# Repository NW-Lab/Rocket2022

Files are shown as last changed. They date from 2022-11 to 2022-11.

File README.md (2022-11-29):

# Rocket2022
発射実験用

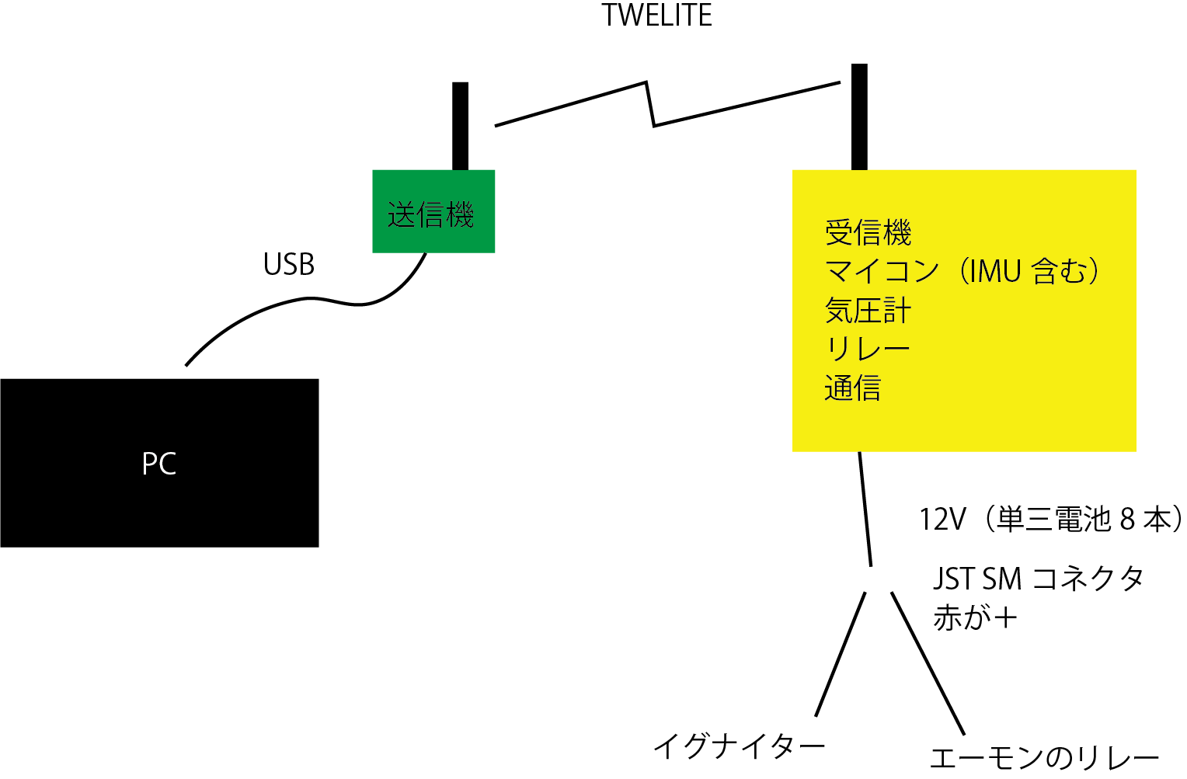
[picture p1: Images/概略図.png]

<br/>
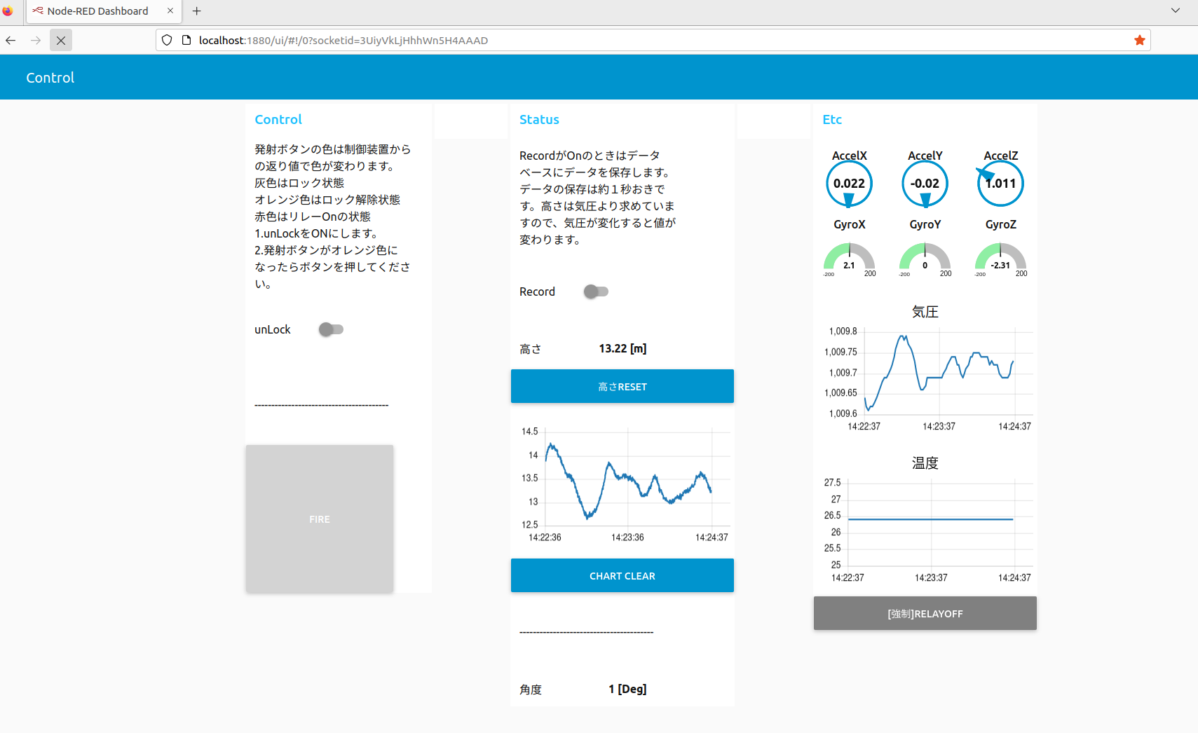
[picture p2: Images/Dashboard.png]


## 使用機材
### PC側
|物品名|規格|URL|備考|
| --- | --- | ---| --- |
|PC|Ubuntu 22.04+NodeRed+InfluxDB| |USB端子があれば|
|TWELITE|TWELITE DIP|https://mono-wireless.com/jp/products/TWE-Lite-DIP/index.html| |
|TWELITE|TWELITE R2|https://mono-wireless.com/jp/products/TWE-LITE-R/index.html| |
|SMA変換ケーブル|MW-C-UJ-10-1|https://mono-wireless.com/jp/products/TWE-ANTENNAS/cables/index.html| |
|防水可倒式アンテナ|MW-A-D114|https://mono-wireless.com/jp/products/TWE-ANTENNAS/dipole/outdoor-ant.html| |
|ケース|タカチ SW‐85B|https://akizukidenshi.com/catalog/g/gP-12472/| |

TWELITEは、普通にUART+適当な変換器(3.3V)でもよかったかも。（TWELITE Stageを設定すると、/dev/ttyUSB0 が見えなくなる。ので設定ソフトとの共用は難しい。無難に設定はWindows機を用意した方が簡単

### ロケット側
|物品名|規格|URL|備考|
| --- | --- | --- | --- |
|マイコン|Seeed Studio XIAO nRF52840 Sense|https://www.seeedstudio.com/Seeed-XIAO-BLE-Sense-nRF52840-p-5253.html|IMU入ってるし、小さいのでこれを選択。あと3.3Vなので（M5は5V)|
|マイコン拡張基板|Seeeduino Xiao用Grove|https://wiki.seeedstudio.com/Grove-Shield-for-Seeeduino-XIAO-embedded-battery-management-chip/|折って4口までにした|
|気圧計|Grove - High Precision Barometric Pressure Sensor (DPS310)|https://www.seeedstudio.com/Grove-High-Precision-Barometer-Sensor-DPS310-p-4397.html|高度が測れる精度が欲しかった|
|リレー|Grobe　Relay|https://www.seeedstudio.com/Grove-Relay.html|3.3Vで動くリレー|
|TWELITE|TWELITE UART|https://mono-wireless.com/jp/products/twelite-uart/index.html|Groveケーブルをはんだ付け|
|SMA変換ケーブル|MW-C-UJ-10-1|https://mono-wireless.com/jp/products/TWE-ANTENNAS/cables/index.html||
|防水可倒式アンテナ|MW-A-D114|https://mono-wireless.com/jp/products/TWE-ANTENNAS/dipole/outdoor-ant.html||
|マイコン用電源（昇圧回路）|電池基板A4-2Unit|https://www.switch-science.com/products/6759|マイコン動作の5Vを簡単にしたかったのでUSBでつないだ|
|発火用電池ボックス|単3x8|https://akizukidenshi.com/catalog/g/gP-00312/||
|バッテリスナップ| |https://akizukidenshi.com/catalog/g/gP-00312/||
|ケース|タカチ　BCPC091208T|https://www.takachi-el.co.jp/products/BCPC||

ねじ少々(M2、M3)

気圧がI2C（D4,D5）、リレーがGPIO（D1,D2）、TWELITEがUART（D6,D7）に接続する。

マイコンと拡張基板が結構ゆるゆるだったのでマスキングテープで補強した。

組み立て<br/>
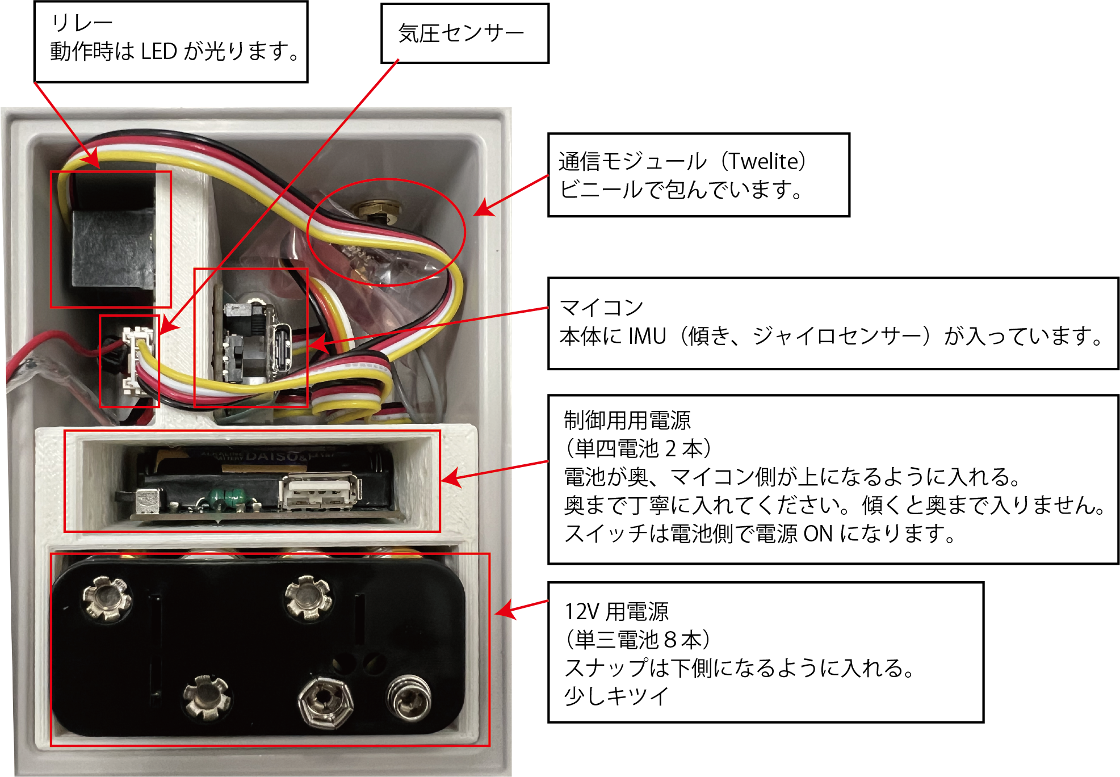
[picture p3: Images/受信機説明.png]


## 開発環境
### PC側
- Ubuntu 20.04LTS
- Node-Red
  - node-red-dashboard
  - node-red-node-serialport
  - node-red-contrib-influxdb
- InfluxDB(OSS) https://www.influxdata.com/
- 
### ロケット側
#### Arduino 1.8.19
Boardは、"Seeed nRF52 mbed enable boards --> Seeed XIAO BLE sense"を利用する。ただし、Board両方Installする必要あり。　https://wiki.seeedstudio.com/XIAO_BLE/

Libraryは以下の2つ
-   Seeed_Arduino_LSM6DS3 Library　https://github.com/Seeed-Studio/Seeed_Arduino_LSM6DS3
-   Adafruit DPS310

## リンク

XIAO BLE https://wiki.seeedstudio.com/XIAO_BLE/

植松電機　https://uematsudenki.com/モデルロケット自作コントローラー/

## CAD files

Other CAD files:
Fusion360/受信機ケース仕切り.f3d
Fusion360/送信機のアンテナ.f3d

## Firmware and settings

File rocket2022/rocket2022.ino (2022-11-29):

#include <Scheduler.h>
#include "LSM6DS3.h"
#include <Adafruit_DPS310.h>
#include "Wire.h"

LSM6DS3 myIMU(I2C_MODE, 0x6A);    //I2C device address 0x6A

Adafruit_DPS310 myDps;
Adafruit_Sensor *dps_temp = myDps.getTemperatureSensor();
Adafruit_Sensor *dps_pressure = myDps.getPressureSensor();

float pressureInit;

//#define mySerial2 SerialUSB
#define mySerial Serial1
#define myRelay D1

//Status
bool sLock = true;
byte RelayCount = 0;
int SensorCount = 0;
byte PcCount = 0;
float sRSSI = 0.0;
float sBattery = 0.0;

//Function
float P2High(float pressure, float pressureInit, float temp) {
  return ((pow((pressureInit / pressure), 1 / 5.257) - 1.0) * (temp + 273.15)) / 0.0065;
}

void setup() {
  int16_t ret;
  mySerial.begin(115200);
  //mySerial2.begin(115200);
  pinMode(myRelay, OUTPUT); digitalWrite(myRelay, LOW);

  pinMode(LEDR, OUTPUT); digitalWrite(LEDR, HIGH);
  pinMode(LEDG, OUTPUT); digitalWrite(LEDG, HIGH);
  pinMode(LEDB, OUTPUT); digitalWrite(LEDB, HIGH);

  if (myIMU.begin() != 0) {
    //mySerial2.println("Device(IMU) error");
  } else {
    //mySerial2.println("Device(IMU) OK!");
  }

  if (! myDps.begin_I2C()) {
    //mySerial2.println("Failed to find DPS");
    while (1) yield();
  }
  //mySerial2.println("DPS310 OK!");
  sensors_event_t  pressure_event;
  myDps.configurePressure(DPS310_128HZ, DPS310_8SAMPLES);
  myDps.configureTemperature(DPS310_128HZ, DPS310_8SAMPLES);
  while ( !myDps.pressureAvailable()) {
    delay(1);
  }
  delay(1000);
  dps_pressure->getEvent(&pressure_event);
  pressureInit = pressure_event.pressure;

  // put your setup code here, to run once:
  Scheduler.startLoop(loop_alive_LED);
  Scheduler.startLoop(loop_Rcv);
  Scheduler.startLoop(loop_Relay);
}

void loop() {
  int16_t ret;
  sensors_event_t temp_event, pressure_event;
  float pressure, temp;
  //Sensor用

/***  
  float ax=myIMU.readFloatAccelX();
  float ay=myIMU.readFloatAccelY();
  float az=myIMU.readFloatAccelZ();
  float gx=myIMU.readFloatGyroX();
  float gy=myIMU.readFloatGyroY();
  float gz=myIMU.readFloatGyroZ();
**/
  float ax=-1.0*myIMU.readFloatAccelY();
  float ay=myIMU.readFloatAccelZ();
  float az=-1.0*myIMU.readFloatAccelX();
  float gx=-1.0*myIMU.readFloatGyroY();
  float gy=myIMU.readFloatGyroZ();
  float gz=-1.0*myIMU.readFloatGyroX();
  
  mySerial.print("{");
  mySerial.print("\"lock\":");
  if (sLock)mySerial.print("true");
  else mySerial.print("false");
  mySerial.print(",\"RelayOn\":");
  if (RelayCount > 0)mySerial.print("true");
  else mySerial.print("false");
  mySerial.println("}");

  mySerial.print("{\"AccelX\":");
  mySerial.print(ax, 3);
  mySerial.print(',');

  mySerial.print("\"AccelY\":");
  mySerial.print(ay, 3);
  mySerial.print(',');

  mySerial.print("\"AccelZ\":");
  mySerial.print(az, 3);
  mySerial.println("}");

  mySerial.print("{\"GyroX\":");
  mySerial.print(gx, 3);
  mySerial.print(',');

  mySerial.print("\"GyroY\":");
  mySerial.print(gy, 3);
  mySerial.print(',');

  mySerial.print("\"GyroZ\":");
  mySerial.print(gz, 3);
  mySerial.println("}");

  while (!myDps.temperatureAvailable() || !myDps.pressureAvailable()) {
    delay(1);
  }
  myDps.getEvents(&temp_event, &pressure_event);
  temp = temp_event.temperature;
  pressure = pressure_event.pressure;

  mySerial.print("{\"Temperature\":");
  mySerial.print(temp, 1);
  mySerial.print(',');

  mySerial.print("\"Pressure\":");
  mySerial.print(pressure, 2);
  mySerial.print(',');

  mySerial.print("\"Height\":");
  mySerial.print(P2High(pressure, pressureInit, temp), 2);
  mySerial.println("}");
  /**
    mySerial.print("{\"RSSI\":");
    mySerial.print(sRSSI, 2);
    mySerial.print(',');

    mySerial.print("\"Battery\":");
    mySerial.print(sBattery, 2);

    mySerial.println("}");
    **/
  delay(100);
}
void loop_alive_LED() {
  // 内蔵LEDは、PullUpされているので反転動作
  if (sLock) {  //ロックされている場合は緑
    digitalWrite(LEDG, LOW);
    digitalWrite(LEDR, HIGH);
    delay(100);
    if (PcCount != 0)digitalWrite(LEDG, HIGH);
    delay(100);
  }
  else {  //ロックが解除されている場合は赤
    digitalWrite(LEDR, LOW);
    digitalWrite(LEDG, HIGH);
    delay(100);
    if (PcCount != 0)digitalWrite(LEDR, HIGH);
    delay(100);
  }
  if (PcCount != 0)PcCount--;
}

void loop_Rcv() {

  if (mySerial.available()) {
    String str = mySerial.readStringUntil('\n');
    str.trim();
    if (str.length() > 0) {
      PcCount = 150; //受信したらPcCountを150(1.5秒)を追加
      str.toLowerCase();//小文字に変換
      if (str.equals("reset")) {
        mySerial.println("!reset");
        //mySerial2.println("**Reset**");
        sensors_event_t  pressure_event;
        while ( !myDps.pressureAvailable()) {
          delay(1);
        }
        dps_pressure->getEvent(&pressure_event);
        pressureInit = pressure_event.pressure;
      }
      else if (str.equals("unlock")) {
        mySerial.println("!unlock");
        //mySerial2.println("**unlock**");
        sLock = false;
      }
      else if (str.equals("lock")) {
        mySerial.println("!lock");
        //mySerial2.println("**lock**");
        sLock = true;
        RelayCount = 0;
      }
      else if (str.equals("relayon")) {
        mySerial.println("!RelayOn");
        //mySerial2.println("**RelayOn**");
        if (!sLock) {
          SensorCount = 150; //15秒
          RelayCount = 30; //3秒
        }
      }
      else if (str.equals("relayoff")) {
        mySerial.println("!RelayOff");
        //mySerial2.println("**RelayOff**");
        RelayCount = 0; //0秒-->Off
        digitalWrite(myRelay, LOW);
      }
      else if (str.equals("fast")) {
        mySerial.println("!fast");
        //mySerial2.println("**fast**");
        SensorCount = 300; //30秒
      }
    }
  }
  delay(100);
//  yield();
}
void loop_Relay() {
  if ((!sLock) && (RelayCount > 0)) {
    digitalWrite(myRelay, HIGH);
    RelayCount--;
  }
  else {
    digitalWrite(myRelay, LOW);
  }
  delay(100);
}

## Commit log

2022-11-17 とりあえずセンサーが動くとこまで
2022-11-17 とりあえず動くとこまで
2022-11-19 バグ修正 Serial --> mySerial
    [rocket2022.ino]
2022-11-22 check用プログラム
2022-11-22 check用プログラム修正
2022-11-25 Update Node-redと組み合せテスト後
2022-11-26 relay-->RelayOn(Boolean)に変更
2022-11-28 BugFix Twelite通信で分かった分
2022-11-29 bug fix(yeild-->delay)
    [受信機ケース仕切り.f3d, 送信機のアンテナ.f3d]
